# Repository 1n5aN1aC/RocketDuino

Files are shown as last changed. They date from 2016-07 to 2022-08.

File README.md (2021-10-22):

# RocketDuino
This is an Arduino Board designed for use in High-Powered model rockets.

(Picture Goes Here)

<h1>Features</h1>

 - Parachute Deployment:  Dual parachute deployment via high-power mosfets to route raw battery current directly through the ignitors.  (Designed for 9v)
 - GPS Tracking: On-board GPS used to verify hight measurements, get speed readouts, and know the location of the rocket.
 - Telemetry: LoRa telemetry transmission with a maximum range of over 8km.  This is used to relay location and height data to a ground control station to ease finding the rocket after parachute deployment.

<h1>Hardware</h1>

 - MCU: Early versions (which were flown successfully) used a wemos D1 mini.  However, the current version uses a Teensy LC as the main microcontroller.  This change was made primarily to take advantage of the multiple hardware serial ports on the Teensy line.
 - GPS:  Works with any Serial GPS device that outputs classic NMEA messages, (GPGGA, etc) does NOT currently support the newer GNGGA messages.  The PCB is designed to directly mount a uBlox NEO-M6N module.  (Note that the config needs to be changes to output GPGGA, etc)
 - Barometer:  A BMP280 is used for more accurate real-time elevation measurement.  Note that the Teensy is NOT 5v compliant, so you need the 3.3v BMP280 board.
 - Telemetry:  Data Transmission is done using a E32-433T30D 1W LoRa trasmitter, but any data transmitter with a serial interface should work, with only minor changes to the board.  (The PCB is designed to mount the module directly.)

<h3>The Board</h3>

Short Description coming soon.

[For Detailed PCB Information, click here](https://github.com/1n5aN1aC/RocketDuino/tree/master/PCB)

<h3>The Software</h3>

Short Description coming soon.

[For Detailed Arduino Information, click here](https://github.com/1n5aN1aC/RocketDuino/tree/master/Arduino)

<h3>The Results</h3>

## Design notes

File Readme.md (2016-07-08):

#PCB files
This is where the files for making the PCBare located.  We use Eagle as our development tool of choice.

##Features
Description Coming Soon!

##Design
Description Coming Soon!

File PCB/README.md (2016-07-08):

#PCB files
This is where the files for making the PCB are located.  We use Eagle as our development tool of choice.

##Features
Description Coming Soon!

##Design
Description Coming Soon!

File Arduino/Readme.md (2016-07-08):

#Arduino files
This is where the files for compiling the flight computer & the ground station are located

##Features
Description Coming Soon!

##Design
Description Coming Soon!

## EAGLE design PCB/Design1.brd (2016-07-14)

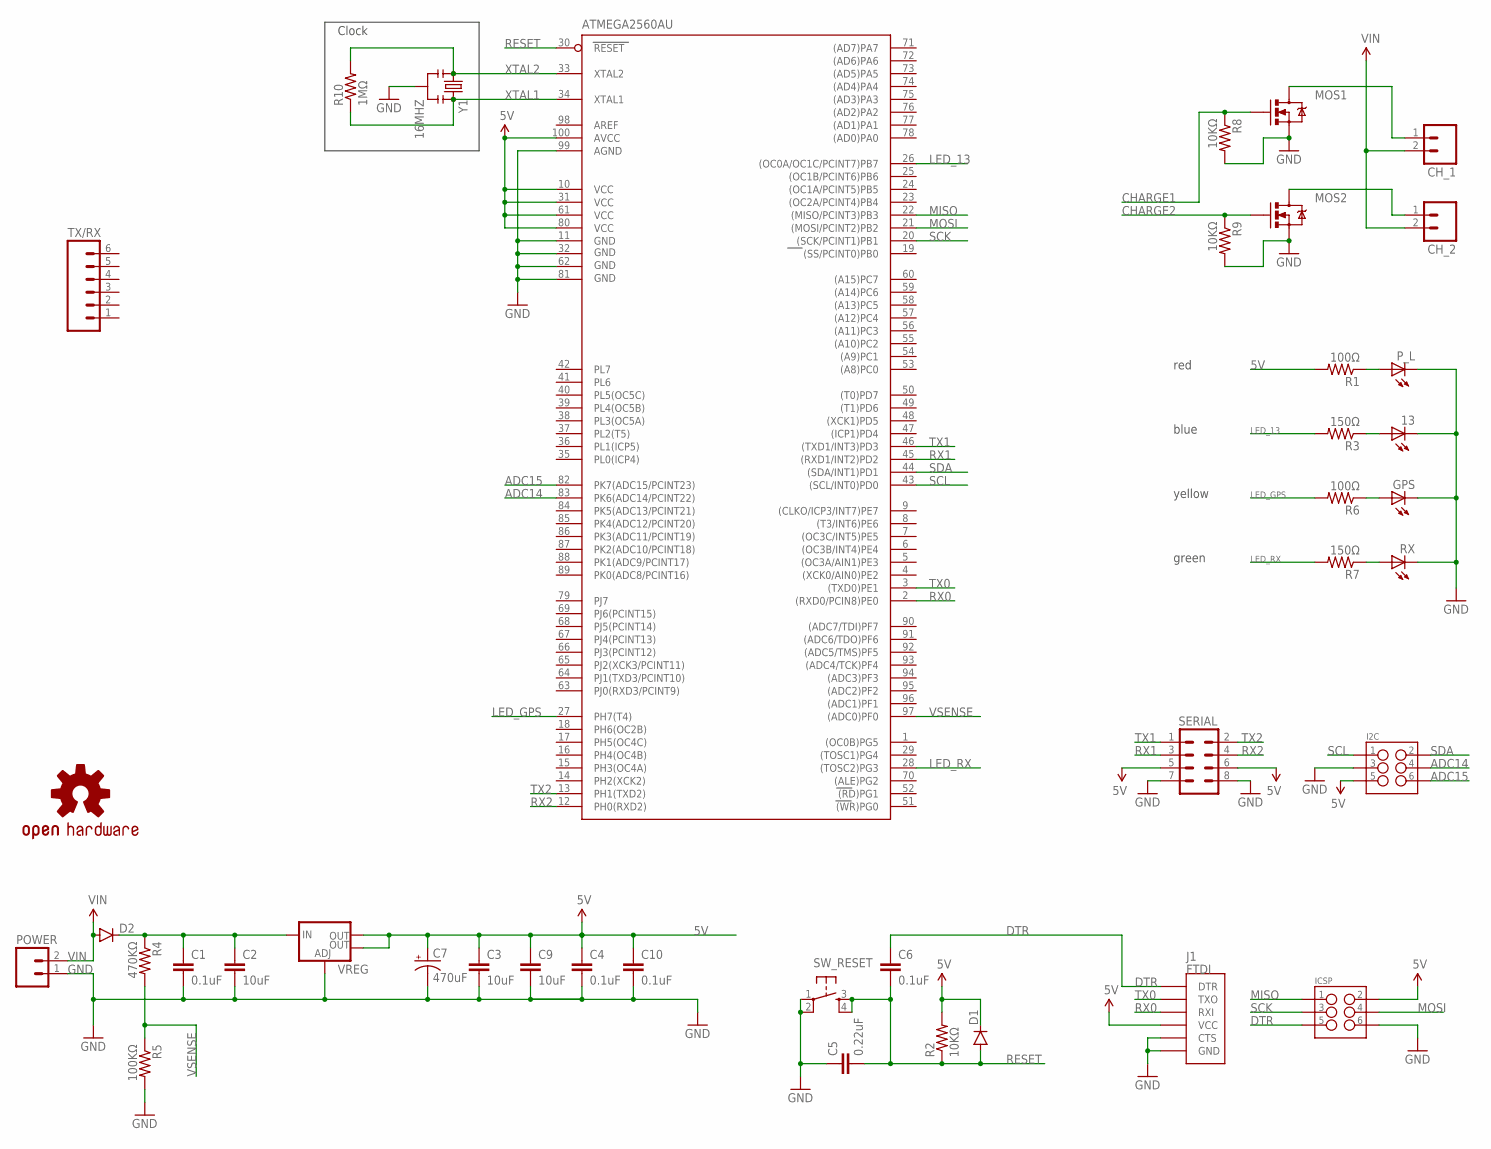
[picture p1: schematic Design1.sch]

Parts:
13: LEDSML0805; SML0805
ATMEGA2560AU: ATMEGA2560AU; TQFP100
C1, C4, C6, C10: 0.1uF; 1206
C2, C3, C9: 10uF; 1206
C5: 0.22uF; 1206
C7: 470uF; CPOL-RADIAL-100UF-25V
CH_1, CH_2: M02LOCK_LONGPADS; 1X02_LOCK_LONGPADS
D1, D2: DIODESMA-ALT; SMA-DIODE_ALT
GPS: LEDSML0805; SML0805
I2C: M03X2FEMALE_SMD; 2X3_SMD
ICSP: M03X2FEMALE_SMD; 2X3_SMD
J1: FTDI; FTDI_DEVICE_SIDE
LOGO1: OSHW-LOGOM; OSHW-LOGO-M
MOS1, MOS2: MOSFET-NCHANNELFQP30N06L; TO220V
POWER: M02LOCK_LONGPADS; 1X02_LOCK_LONGPADS
P_L: LEDSML0805; SML0805
R1, R6: 100Ω; 1206
R2, R8, R9: 10KΩ; 1206
R3, R7: 150Ω; 1206
R4: 470KΩ; 1206
R5: 100KΩ; 1206
R10: 1MΩ; 1206
RX: LEDSML0805; SML0805
SERIAL: M04X2; 2X4
SW_RESET: SWITCH_SPST_4_PINSQUARE; TACTILE-SWITCH-SMD
TX/RX: M06SILK_FEMALE_PTH; 1X06
VREG: V_REG_LM1117SOT223; SOT223
Y1: 16MHZ; RESONATOR-SMD

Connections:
5V: ATMEGA2560AU.10 (VCC), ATMEGA2560AU.31 (VCC1), ATMEGA2560AU.61 (VCC2), ATMEGA2560AU.80 (VCC3), ATMEGA2560AU.100 (AVCC), C3.1, C4.1, C7.1 (+), C9.1, C10.1, D1.C, I2C.5, ICSP.2, J1.P$4 (VCC), R1.2, R2.2, SERIAL.5, SERIAL.6, VREG.2 (OUT), VREG.4 (OUT)
ADC14: ATMEGA2560AU.83 (PK6(ADC14/PCINT22)), I2C.4
ADC15: ATMEGA2560AU.82 (PK7(ADC15/PCINT23)), I2C.6
CHARGE1: MOS1.1 (G), R8.1
CHARGE2: MOS2.1 (G), R9.1
DTR: C6.1, ICSP.5, J1.P$1 (DTR)
GND: 13.C, ATMEGA2560AU.11 (GND), ATMEGA2560AU.32 (GND1), ATMEGA2560AU.62 (GND2), ATMEGA2560AU.81 (GND3), ATMEGA2560AU.99 (AGND), C1.2, C2.2, C3.2, C4.2, C5.1, C7.2 (-), C9.2, C10.2, GPS.C, I2C.3, ICSP.6, J1.P$5 (CTS), J1.P$6 (GND), MOS1.3 (S), MOS2.3 (S), POWER.1, P_L.C, R5.2, R8.2, R9.2, RX.C, SERIAL.7, SERIAL.8, SW_RESET.1, SW_RESET.2, VREG.1 (ADJ), Y1.2
LED_13: ATMEGA2560AU.26 ((OC0A/OC1C/PCINT7)PB7), R3.2
LED_GPS: ATMEGA2560AU.27 (PH7(T4)), R6.2
LED_RX: ATMEGA2560AU.28 ((TOSC2)PG3), R7.2
MISO: ATMEGA2560AU.22 ((MISO/PCINT3)PB3), ICSP.1
MOS1: CH_1.1, MOS1.2 (D)
MOS2: CH_2.1, MOS2.2 (D)
MOSI: ATMEGA2560AU.21 ((MOSI/PCINT2)PB2), ICSP.4
unnamed: GPS.A, R6.1
unnamed: P_L.A, R1.1
unnamed: 13.A, R3.1
unnamed: R7.1, RX.A
RESET: ATMEGA2560AU.30 (RESET), C5.2, C6.2, D1.A, R2.1, SW_RESET.3, SW_RESET.4
RX0: ATMEGA2560AU.2 ((RXD0/PCIN8)PE0), J1.P$3 (RXI)
RX1: ATMEGA2560AU.45 ((RXD1/INT2)PD2), SERIAL.3
RX2: ATMEGA2560AU.12 (PH0(RXD2)), SERIAL.4
SCK: ATMEGA2560AU.20 ((SCK/PCINT1)PB1), ICSP.3
SCL: ATMEGA2560AU.43 ((SCL/INT0)PD0), I2C.1
SDA: ATMEGA2560AU.44 ((SDA/INT1)PD1), I2C.2
TX0: ATMEGA2560AU.3 ((TXD0)PE1), J1.P$2 (TXO)
TX1: ATMEGA2560AU.46 ((TXD1/INT3)PD3), SERIAL.1
TX2: ATMEGA2560AU.13 (PH1(TXD2)), SERIAL.2
VIN: CH_1.2, CH_2.2, D2.A, POWER.2
VIN_RECTIFIED: C1.1, C2.1, D2.C, R4.1, VREG.3 (IN)
VSENSE: ATMEGA2560AU.97 ((ADC0)PF0), R4.2, R5.1
XTAL1: ATMEGA2560AU.34 (XTAL1), R10.1, Y1.3
XTAL2: ATMEGA2560AU.33 (XTAL2), R10.2, Y1.1

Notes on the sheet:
Clock
green
yellow
blue
red

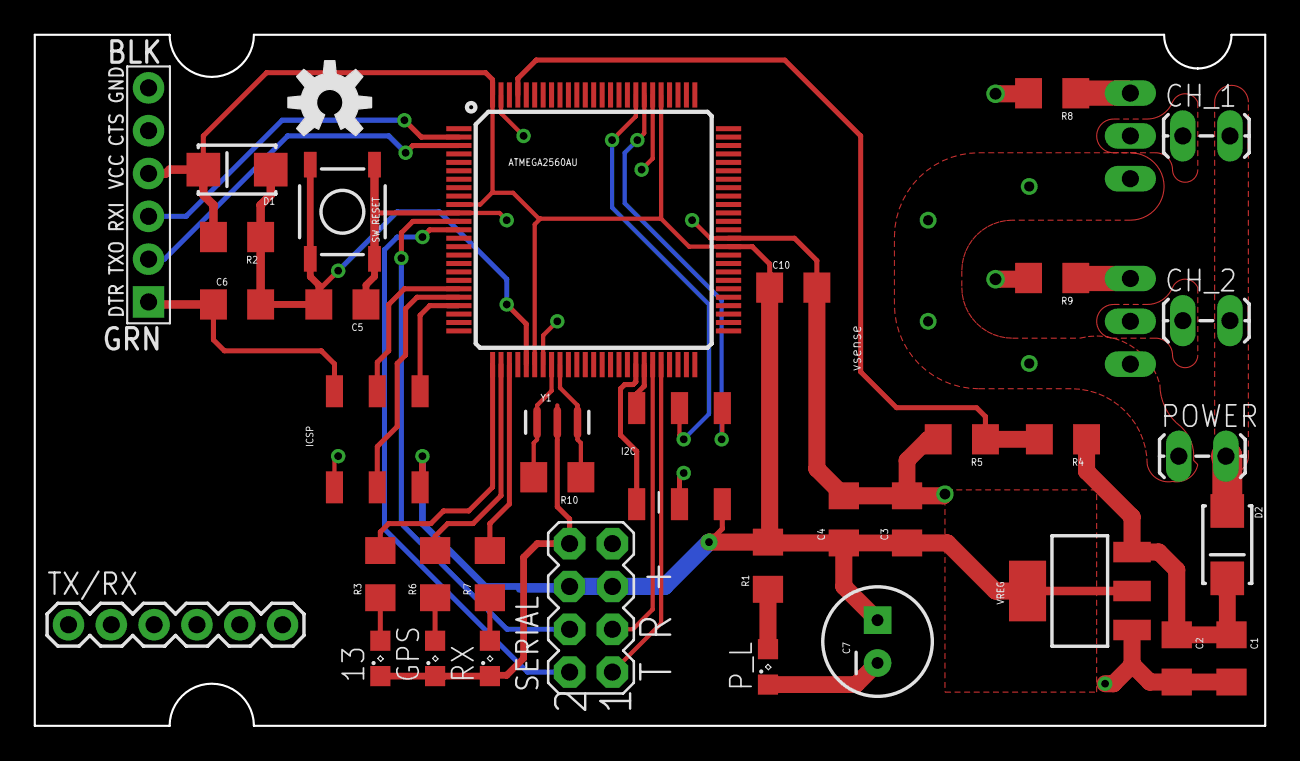
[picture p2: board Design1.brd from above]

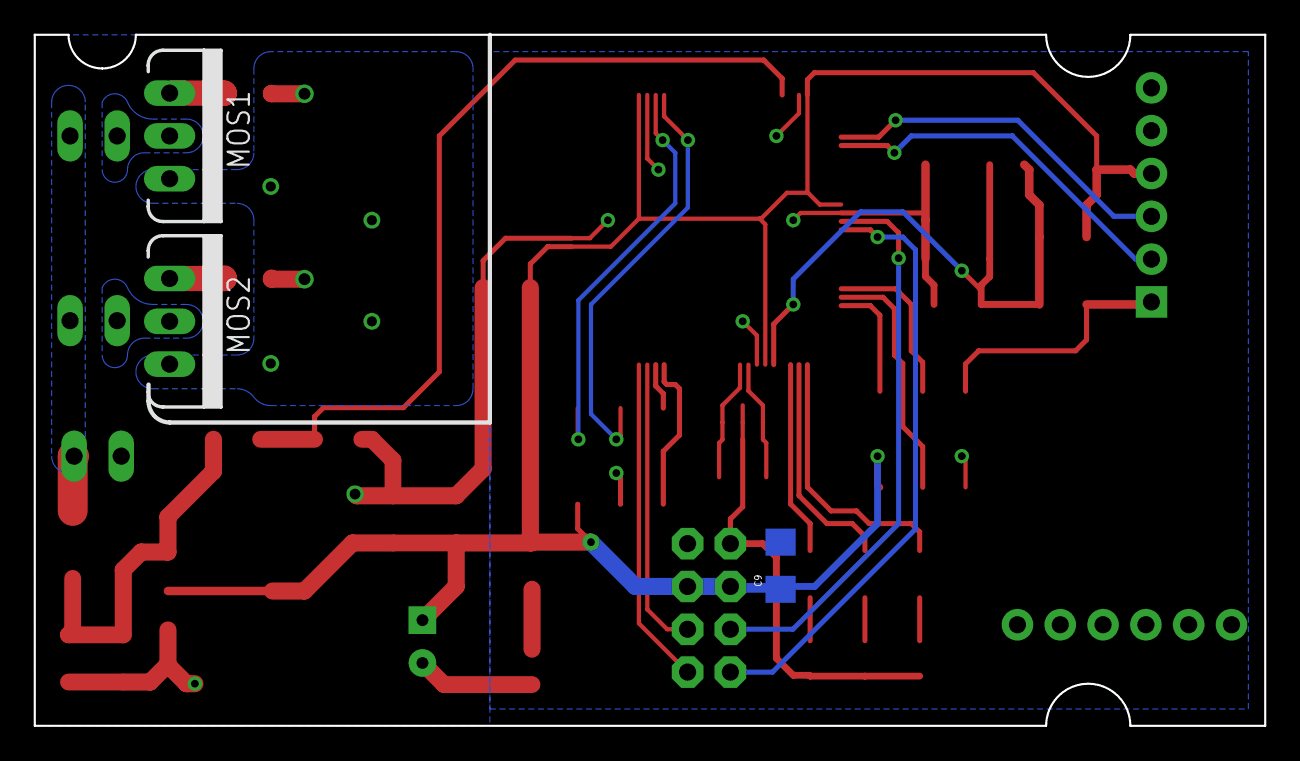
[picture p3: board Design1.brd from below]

Board: 2 copper layers, 73.0 x 41.0 mm, 40 parts (3 on the bottom side), 33 nets.

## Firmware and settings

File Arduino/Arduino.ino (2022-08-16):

//
// File:    main.ino
// Author:  1n5aN1aC (Joshua Villwock)
// Purpose: Handles all logic for the RocketDuino
//
// TODO:
// 1. Increase transmission power to maximum.  (is min right now)
// 2. Mode for Serial Passthrough to GPS.  (To upload sat info, etc.)
//

#include "Arduino.h"
#include <Wire.h>
#include <BMP280_DEV.h>
#include <SimpleKalmanFilter.h>
#include <TinyGPS++.h>

//LoRa Hardware parameters
#define E32_TTL_1W
#define FREQUENCY_433
#include "LoRa_E32.h"

// Pin designations
#define BUZZER 17 //Buzzer Pin
#define CHUTE1 6  //Output for Chute Channel 1
#define CHUTE2 5  //Output for Chute Channel 2
#define LED    13 //Teensy Onboard LED
#define LED1   4  //PCB LED 1 (Green)
#define LED2   3  //PCD LED 2 (Yellow)
#define LORARX 9  //Lora_RX  (E32TX)
#define LORATX 10 //Lora_TX  (E32RX)
#define LORAUX 8  //Lora_AUX (Status)
#define LORAM0 12 //Lora_M0  (Mode Set)
#define LORAM1 11 //Lora_M1  (Mode Set)
//GPS  = Serial1
//Lora = Serial2

// Barometer Variables
BMP280_DEV bmp280; // Define barometer object. Basic I2C SCL & SDA
SimpleKalmanFilter altitudeFilterObject(4, 1, 0.015); //Measurement Uncertainty, Estimation Uncertainty, Noise
float    temporaryAltitude       = 0;
float    currentFilteredAltitude = 0;
elapsedMillis lastBarometerRead;

// Mode variables
#define  FREQUENCY_UPDATE_MODE   250
uint8_t  currentMode             = 0;
elapsedMillis lastModeUpdate;

// Buzzer Variables
#define  FREQUENCY_UPDATE_BUZZER 3000
elapsedMillis lastBuzzerUpdate;

// Serial Variables
#define  FREQUENCY_TX_LORA       1000
elapsedMillis lastLoraTX;
LoRa_E32 e32ttl100(LORARX, LORATX, LORAUX, LORAM0, LORAM1, UART_BPS_RATE_9600);

// GPS Variables
TinyGPSPlus   gps;
TinyGPSCustom gpsStatus(gps, "GPGGA", 6);
#define  GPSBAUDRATE             115200
unsigned char extraSerialBuffer  [300];   //extra memory to dedocate to gps rx
int sizeOfExtraSerialBuffer      = 300;
bool     GPSforward              = false;
elapsedMillis lastGPSReceive;

struct __attribute__((packed)) packet_normal {
  uint32_t timeStamp;         //4 bytes
  uint8_t  currentMode;       //1 byte
  int16_t  currentAlt;        //2 bytes
  int16_t  startingAlt;       //2 bytes
  int16_t  maxAlt;            //2 bytes
  
  double   latitude;          //8 bytes
  double   longitude;         //8 bytes
  uint16_t gpsAlt;            //2 bytes
  uint16_t gpsSpeedMPS;       //2 bytes
  uint8_t  gpsSats;           //1 byte
  uint16_t gpsHDOP;           //2 bytes
  uint8_t  gps_mode;          //1 byte (only 2 bits needed)
  uint8_t  gps_valid;         //1 byte (only 1 bit needed)
  uint16_t gps_receivedSents; //2 bytes
  uint8_t  gps_checkFails;    //1 byte
  uint8_t  checksum;          //1 byte
};                   //TOTAL = 40 bytes, maximum 51 / 58 Bytes   (58 on-air) [Must wait 3-byte time between packets if <58bytes]

// Init Values
int16_t  maxAltitudeSeen    = -32768;   //Highest we've been to
int16_t  startingAltitude   = 0;   //what elevation we consider 'ground'
uint16_t failsafeAltitude   = 100; //minimum alt we need to reach to arm
uint8_t  extraDeploymentAlt = 25;  //Extra meters we have to fall below max alt before deployment (to be safe from jiggle)

//
// Run Initial setup Tasks
//
void setup() {
  // Init variables & objects
  pinMode(BUZZER, OUTPUT);
  pinMode(CHUTE1, OUTPUT);
  pinMode(CHUTE2, OUTPUT);
  pinMode(LED,    OUTPUT);
  pinMode(LED1,   OUTPUT);
  pinMode(LED2,   OUTPUT);
  pinMode(LORAM0, OUTPUT);
  pinMode(LORAM1, OUTPUT);
  digitalWrite(LED,    HIGH);  //LED on startup

  //Init USB serial port
  Serial.begin(57600); //USB
  Serial.println(F("[SER]  (USB)    Debug serial began.  (57600)"));

  //Init GPS serial port
  Serial1.begin(GPSBAUDRATE);
  Serial.println(F("[SER]  (GPS)    Gps serial began.") + String(GPSBAUDRATE) + ")");
  //We need to dedicate extra memory to the GPS receive buffer:
  Serial1.addMemoryForRead(extraSerialBuffer, sizeOfExtraSerialBuffer);

  //Init lora transmitter
  setup_LoRa();

  //Init Baro
  Serial.println(F("[BARO] (Config) Configuring Altimiter..."));
  bmp280.begin(SLEEP_MODE, BMP280_I2C_ALT_ADDR);  // Default initialisation with alternative I2C address (0x76), place the BMP280 into SLEEP_MODE
  bmp280.setPresOversampling(OVERSAMPLING_X2);    // Options are OVERSAMPLING_SKIP, _X1, _X2, _X4, _X8, _X16
  bmp280.setTempOversampling(OVERSAMPLING_X1);    // Options are OVERSAMPLING_SKIP, _X1, _X2, _X4, _X8, _X16
  bmp280.setIIRFilter(IIR_FILTER_OFF);            // Options are IIR_FILTER_OFF, _2, _4, _8, _16
  bmp280.setTimeStandby(TIME_STANDBY_62MS);       // Options are TIME_STANDBY_05MS, _62MS, _125MS, _250MS, _500MS, _1000MS, 2000MS, 4000MS
  bmp280.startNormalConversion();                 // Start BMP280 continuous conversion in NORMAL_MODE

  delay(500); //Wait for stuff to init
  digitalWrite(LED, LOW);  //LED off as startup finished
  Serial.println("[Info]          Start up Complete.");
}

void setup_LoRa() {
  //Serial2.begin(LORABAUDRATE);
  //Serial.println("LORA Serial Started" + String(LORABAUDRATE) + ")");

  //Connect to module
  Serial.println(F("[LoRa] (Config) Connecting to module..."));  // https://www.mischianti.org/2019/10/21/lora-e32-device-for-arduino-esp32-or-esp8266-library-part-2/
  e32ttl100.begin();                                             // Startup all pins and UART
  delay(200);

  //Fetch LoRa module information
  ResponseStructContainer cMi;
  cMi = e32ttl100.getModuleInformation();
  ModuleInformation mi = *(ModuleInformation*)cMi.data; // It's important get information pointer before all other operation
  cMi.close();
  Serial.print(F("[LoRa] (Config) Version:  "));
  Serial.println(mi.version, HEX);
  Serial.print(F("[LoRa] (Config) Features: "));
  Serial.println(mi.features, HEX);

  Serial.println(F("[LoRa] (Config) Fetching current config..."));
  ResponseStructContainer c;                                     // C stores the config
  c = e32ttl100.getConfiguration();                              // Load config from module
  Configuration configuration = *(Configuration*) c.data;        // Make local config object
  int numChanges = 0;

  //Communication channel (def 17H == 23d == 433MHz / 410 M + CHAN*1M)
  Serial.print(F("[LoRa] (Config) Communication channel: "));
  Serial.print(configuration.CHAN, HEX);
  Serial.print(F(" Wants: "));
  Serial.print(0x17, HEX);
  if (configuration.CHAN != 0x17) {
    configuration.CHAN = 0x17;
    numChanges++;
    Serial.print(F(" OPTION UPDATED."));
  }
  Serial.println();

  //Forward Error Correction
  Serial.print(F("[LoRa] (Config) FEC: "));
  Serial.print(configuration.OPTION.fec);
  Serial.print(F(" Wants: "));
  Serial.print(FEC_1_ON);
  if (configuration.OPTION.fec != FEC_1_ON) {
    configuration.OPTION.fec = FEC_1_ON;
    numChanges++;
    Serial.print(F(" OPTION UPDATED."));
  }
  Serial.println();

  //Broadcast/directed setting
  Serial.print(F("[LoRa] (Config) Fixed/Transparent: "));
  Serial.print(configuration.OPTION.fixedTransmission);
  Serial.print(F(" Wants: "));
  Serial.print(FT_FIXED_TRANSMISSION);
  if (configuration.OPTION.fixedTransmission != FT_FIXED_TRANSMISSION) {
    configuration.OPTION.fixedTransmission = FT_FIXED_TRANSMISSION;
    numChanges++;
    Serial.print(F(" OPTION UPDATED."));
  }
  Serial.println();

  //Pull ups enabled or not
  Serial.print(F("[LoRa] (Config) Pull-ups: "));
  Serial.print(configuration.OPTION.ioDriveMode);
  Serial.print(F(" Wants: "));
  Serial.print(IO_D_MODE_PUSH_PULLS_PULL_UPS);
  if (configuration.OPTION.ioDriveMode != IO_D_MODE_PUSH_PULLS_PULL_UPS) {
    configuration.OPTION.ioDriveMode = IO_D_MODE_PUSH_PULLS_PULL_UPS;
    numChanges++;
    Serial.print(F(" OPTION UPDATED."));
  }
  Serial.println();

  //dBm transmission power (POWER_30 POWER_27 POWER_24 POWER_21)
  Serial.print(F("[LoRa] (Config) TX Power: "));
  Serial.print(configuration.OPTION.transmissionPower);
  Serial.print(F(" Wants: "));
  Serial.print(POWER_21);
  if (configuration.OPTION.transmissionPower != POWER_21) {
    configuration.OPTION.transmissionPower = POWER_21;
    numChanges++;
    Serial.print(F(" OPTION UPDATED."));
  }
  Serial.println();

  //Wait time for wake up
  Serial.print(F("[LoRa] (Config) Wake time: "));
  Serial.print(configuration.OPTION.wirelessWakeupTime);
  Serial.print(F(" Wants: "));
  Serial.print(WAKE_UP_250);
  if (configuration.OPTION.wirelessWakeupTime != WAKE_UP_250) {
    configuration.OPTION.wirelessWakeupTime = WAKE_UP_250;
    numChanges++;
    Serial.print(F(" OPTION UPDATED."));
  }
  Serial.println();

  //Air data rate (2.4k)
  Serial.print(F("[LoRa] (Config) Air data rate: "));
  Serial.print(configuration.SPED.airDataRate);
  Serial.print(F(" Wants: "));
  Serial.print(AIR_DATA_RATE_010_24);
  if (configuration.SPED.airDataRate != AIR_DATA_RATE_010_24) {
    configuration.SPED.airDataRate = AIR_DATA_RATE_010_24;
    numChanges++;
    Serial.print(F(" OPTION UPDATED."));
  }
  Serial.println();

  //Serial baud rate
  Serial.print(F("[LoRa] (Config) Serial Baud: "));
  Serial.print(configuration.SPED.uartBaudRate);
  Serial.print(F(" Wants: "));
  Serial.print(UART_BPS_9600);
  if (configuration.SPED.uartBaudRate != UART_BPS_9600) {
    configuration.SPED.uartBaudRate = UART_BPS_9600;
    numChanges++;
    Serial.print(F(" OPTION UPDATED."));
  }
  Serial.println();

  //Serial UART Parity
  Serial.print(F("[LoRa] (Config) Serial Parity: "));
  Serial.print(configuration.SPED.uartParity);
  Serial.print(F(" Wants: "));
  Serial.print(MODE_00_8N1);
  if (configuration.SPED.uartParity != MODE_00_8N1) {
    configuration.SPED.uartParity = MODE_00_8N1;
    numChanges++;
    Serial.print(F(" OPTION UPDATED."));
  }
  Serial.println();

  //Address(high)
  Serial.print(F("[LoRa] (Config) Address (high): "));
  Serial.print(configuration.ADDH);
  Serial.print(F(" Wants: "));
  Serial.print(13);
  if (configuration.ADDH != 13) {
    configuration.ADDH = 13;
    numChanges++;
    Serial.print(F(" OPTION UPDATED."));
  }
  Serial.println();

  //Address(low)
  Serial.print(F("[LoRa] (Config) Address (low): "));
  Serial.print(configuration.ADDL);
  Serial.print(F(" Wants: "));
  Serial.print(13);
  if (configuration.ADDL != 13) {
    configuration.ADDL = 13;
    numChanges++;
    Serial.print(F(" OPTION UPDATED."));
  }
  Serial.println();

  if (numChanges > 0) {
    Serial.println(F("[LoRa] (Config) Setting new config..."));
    e32ttl100.setConfiguration(configuration, WRITE_CFG_PWR_DWN_SAVE); // Save config permanently
    delay(500); //Wait for stuff to save and such
  } else {
    Serial.println(F("[LoRa] (Config) No config changes to save..."));
  }
  c.close();                                                         // Must close after opening

  delay(300); //Wait for stuff to init
  Serial.println(F("[LoRa] (Config) Complete."));
}

//
// Main Loop Tasks
//
void loop() {
  //Gather new (baro) data
  update_barometer();

  //Calculate on data (flight modes)
  calculate_mode();

  //Update Serial / wireless
  update_lora_send();

  //Handle incoming gps data
  update_gps_receive();

  //Handle incoming lora packets
  update_lora_receive();

  //Update buzzer / LEDs
  update_buzzer();
}

//
// Queries the barometer for elevation, stores it, and updates the running average
void update_barometer() {
  if (bmp280.getAltitude(temporaryAltitude)) {   // Check if the measurement is complete
    currentFilteredAltitude = altitudeFilterObject.updateEstimate(temporaryAltitude);

    //Update max altitude if needed and out of startup mode
    if (currentMode > 0 && currentFilteredAltitude > maxAltitudeSeen) {
      maxAltitudeSeen = currentFilteredAltitude;
    }

    //Take note that we've sucessfully read the altitude:
    lastBarometerRead = 0;
  }
}

//
// Mode 0 = Boot
// Mode 1 = Below Failsafe Alt
// Mode 2 = Flying
// Mode 3 = Eject!
//
void calculate_mode() {
  if (lastModeUpdate > FREQUENCY_UPDATE_MODE) {
    lastModeUpdate = 0;

    // Mode 0 = Boot
    if (currentMode == 0) {
      //Once 20 seconds have passed on boot, lets call that the starting height.
      if (millis() > 30000) {
        startingAltitude = currentFilteredAltitude;
        currentMode = 1;
        Serial.println(F("[MODE] (Change) Mode 0->1"));
        digitalWrite(LED, LOW); //Onboard LED
      }
      //Also, if we haven't read the barometer recently, abort:
      if (millis() > 5000 && lastBarometerRead > 5000) {
        Serial.println(F("[ERROR]         More than 5000ms since last baro read!"));
        tone(BUZZER, 4000);
        digitalWrite(LED, HIGH);  //LED on error
        delay(90000);
      }
      return;
    }

    //Mode 1 = Below Failsafe Alt
    if (currentMode == 1) {
      //If we are above the failsafe height, go to flight mode.
      if (currentFilteredAltitude > startingAltitude + failsafeAltitude) {
        currentMode = 2;
        Serial.println(F("[MODE] (Change) Mode 1->2"));
      }
      return;
    }

    //Mode 2 = Flying
    if (currentMode == 2) {
      //If we're more than the safety distance below max alt, go to eject mode
      if (maxAltitudeSeen > currentFilteredAltitude + extraDeploymentAlt) {
        //WAIT!! If we're below the failsafe altitude, don't.
        if (currentFilteredAltitude < startingAltitude + failsafeAltitude) {
          return;
        }
        currentMode = 3;
        Serial.println(F("[MODE] (Change) Mode 2->3"));
        digitalWrite(CHUTE1, HIGH);
        digitalWrite(CHUTE2, HIGH);
        delay(500);
        digitalWrite(CHUTE1, LOW);
        digitalWrite(CHUTE2, LOW);
      }
      return;
    }

    //Mode 3 = Eject & Recovery
    if (currentMode == 3) {
      //We're already done, so do nothing I guess?
    }
  }
}

//Process any incoming bytes from the GPS
void update_gps_receive() {
  while (Serial1.available()) {
    gps.encode(Serial1.read());
    lastGPSReceive = 0;
  }
}

// Buzzes depending on current mode
// Updates GPSmode led
// Updates flight mode LED
void update_buzzer() {
  if (lastBuzzerUpdate > FREQUENCY_UPDATE_BUZZER) {
    //Update buzzer
    lastBuzzerUpdate = 0;
    if (currentMode == 0) {
      digitalWrite(LED1, HIGH); // Status LED on for duration
      tone(BUZZER, 2000, 75);   // Send 2KHz sound signal for 75ms
      delay(125);
      tone(BUZZER, 4000, 75);   // Send 4KHz sound signal for 75ms
      delay(125);
      tone(BUZZER, 2000, 25);   // Send 2KHz sound signal for 25ms
      digitalWrite(LED1, LOW);
    } else if (currentMode == 1) {
      digitalWrite(LED1, HIGH); // Status LED on
      tone(BUZZER, 4000, 25);   // Send 4KHz sound signal for 25ms
    } else if (currentMode == 3) {
      digitalWrite(LED1, LOW);  // Status LED off
      tone(BUZZER, 4000, 100);  // Send 4KHz sound signal for 100ms
      delay(200);
      tone(BUZZER, 4000, 100);  // Send 4KHz sound signal for 100ms
    }

    //Update GPSmode LED
    uint8_t gps_mode;
    if (gps.location.age() > 1500) {
      gps_mode = 0;
    } else {
      gps_mode = atoi(gpsStatus.value());
    }
    if (gps_mode == 2) {        //DGPS
      digitalWrite(LED2, HIGH);
    } else if (gps_mode == 1) { //2D-3D Fix
      bool current = digitalRead(LED2);
      if (current) {
        digitalWrite(LED2, LOW);
      } else {
        digitalWrite(LED2, HIGH);
      }
    } else {                    //No fix
      digitalWrite(LED2, LOW);
    }
  }
}

void update_lora_receive() {
  while (Serial2.available()) {
    byte b = Serial2.read();
  }
}

void update_lora_send() {
  if (lastLoraTX > FREQUENCY_TX_LORA) {
    lastLoraTX = 0;

    send_packet_normal();
  }
}

void send_packet_normal() {
  //When was the last time we got GPS packets?
  uint8_t gps_valid = 0;
  if (gps.altitude.age() > 1050) {
    gps_valid += 1;    //TinyGPS++ says it wasn't updated within last second.
  }
  if (lastGPSReceive > 1000) {
    gps_valid += 2;    //We haven't received any gps serial to even pass it on to TinyGPS++.
  }
  if (!gps.altitude.isValid()) {
    gps_valid += 4;    //Something wrong with the altitude fix?
  }

//  Serial.print(F("[DEBUG] "));
//  Serial.print(static_cast<int16_t>(currentFilteredAltitude));
//    Serial.print(",");
//  Serial.print(maxAltitudeSeen);
//    Serial.print(",");
//  Serial.print(startingAltitude);
//    Serial.print(",");
//  Serial.print(currentMode);
//    Serial.print(",");
//  Serial.print(gps.location.lat());
//    Serial.print(",");
//  Serial.print(gps.location.lng());
//    Serial.print(",");
//  Serial.print(gps.altitude.meters());
//    Serial.print(",");
//  Serial.print(gps.speed.mps());
//    Serial.print(",");
//  Serial.print(gps.satellites.value());
//    Serial.print(",");
//  Serial.print(static_cast<int16_t>(gps.hdop.value()));
//    Serial.print(",");
//  Serial.print(gpsStatus.value());
//    Serial.print(",");
//  Serial.print(gps_valid);
//  Serial.println();

  packet_normal packet = {
    millis(),
    currentMode,
    static_cast<int16_t>(currentFilteredAltitude),
    startingAltitude,
    maxAltitudeSeen,
    gps.location.lat(),
    gps.location.lng(),
    static_cast<uint16_t>(gps.altitude.meters()),
    static_cast<uint16_t>(gps.speed.mps()),
    static_cast<uint8_t> (gps.satellites.value()),
    static_cast<uint16_t>(gps.hdop.value()),
    static_cast<uint8_t> (String(gpsStatus.value()).toInt()),
    gps_valid,
    static_cast<uint16_t>(gps.passedChecksum()),
    static_cast<uint8_t> (gps.failedChecksum()),
    0 //checksum
  };
  //Serial.println(sizeof(packet));

  //Calculate checksum and add to packet
  uint8_t sum = 0;
  uint8_t *p = (uint8_t *)&packet;
  for (uint8_t i=0; i<sizeof(packet); i++) {
      sum += p[i];
  }
  packet.checksum = sum;

  //Serial.write(reinterpret_cast<char*>(&packet), sizeof packet);
  //Serial2.write(reinterpret_cast<char*>(&packet), sizeof packet);
  e32ttl100.sendFixedMessage(0,3,0x17,&packet, sizeof(packet));
}

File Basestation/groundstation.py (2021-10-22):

#!/usr/bin/python
import signal, sys, time, os, datetime
import serial, curses, pickle
import bitstring, numpy
import matplotlib.pyplot as plt

ser = serial.Serial(port='com5', baudrate=57600, timeout=0.1)
ser.flushInput()

data_dict = {'altitude':0, 'altitude_starting':0, 'altitude_max':0,'mode':0}
data_dict['gps'] = {'altitude':0, 'lat':0, 'long':0, 'speed':0, 'sats':0, 'mode':0, 'recent':0}
data_dict['ground_stats'] = {'num_pks_basic':0, 'num_pks_gps':0, 'num_pks_extra':0, 'num_pks_unknown':0}

#logfile naming
dt = datetime.datetime.now()
fileName = 'Data-%s-%s-%s_%s-%s-%s.csv' % (dt.year, dt.month, dt.day, dt.hour, dt.minute, dt.second)
log_file = open(fileName, "w")

last_basic   = time.time()
last_gps     = time.time()
last_extra   = time.time()
last_unknown = time.time()

#adjust these values based on your location and map, lat and long are in decimal degrees
#TRX = -123.33515659247273 #top right longitude
#TRY = 44.983171093204625  #top right latitude
#BLX = -123.33956613486257 #bottom left longitude
#BLY = 44.98096497612233   #bottom left latitude
TRX = -123.3367622         #top right longitude
TRY = 45.0113628           #top right latitude
BLX = -123.3450571         #bottom left longitude 0.006611
BLY = 45.0073493           #bottom left latitude  0.0027238
last_lat = TRY

#Set up the Map:
plt.ion #interactive mode
#im = plt.imread('home.png') #lay the image under the graph
im = plt.imread('buhler.png') #lay the image under the graph
implot = plt.imshow(im,extent=[BLX, TRX, BLY, TRY]) #read a png file to map on
#Joshua:
path_collection = []
plt.draw()
plt.pause(0.05) #is necessary for the plot to update for some reason

def update_screen(screen):
	screen.clear()
	screen.border(0)
	
	#Header
	screen.addstr(2, 4, "RocketDuino Ground Control Station", curses.color_pair(1))
	screen.addstr(3, 16, "v 0.2.1", curses.color_pair(1))
	
	#Mode
	screen.addstr(6, 6, "MODE:      ", curses.color_pair(2))
	screen.addstr(6, 17, str(data_dict['mode']))
	if   data_dict['mode'] == 0:
		screen.addstr(6, 19, str("(Warmup)"), curses.color_pair(7))
	elif data_dict['mode'] == 1:
		screen.addstr(6, 19, str("(Ready)"), curses.color_pair(6))
	elif data_dict['mode'] == 2:
		screen.addstr(6, 19, str("(Flying)"), curses.color_pair(8))
	elif data_dict['mode'] == 3:
		screen.addstr(6, 19, str("(Recovery)"), curses.color_pair(7))
	
	screen.addstr(7, 6, "GPS MODE:  ", curses.color_pair(2))
	screen.addstr(7, 17, str(data_dict['gps']['mode']))
	#GpsMode:
	if   data_dict['gps']['mode'] == 0:
		screen.addstr(7, 19, str("(No Fix)"), curses.color_pair(7))
	elif data_dict['gps']['mode'] == 1:
		screen.addstr(7, 19, str("(2D/3D)"), curses.color_pair(8))
	elif data_dict['gps']['mode'] == 2:
		screen.addstr(7, 19, str("(DGPS)"), curses.color_pair(6))
	elif data_dict['gps']['mode'] == 3:
		screen.addstr(7, 19, str("(Bad Fix)"), curses.color_pair(7))
	screen.addstr(" (" + str(data_dict['gps']['sats']) + " sats) ", curses.color_pair(3))
	
	#GpsRecent:
	if   data_dict['gps']['recent'] == 0:
		screen.addstr(str("(GPS Disconnected)"), curses.color_pair(7))
	
	#Altitude measurements:
	screen.addstr(10, 6, "max alt:   ", curses.color_pair(2))
	screen.addstr(11, 6, "altitude:  ", curses.color_pair(2))
	screen.addstr(12, 6, "start alt: ", curses.color_pair(2))
	
	screen.addstr(10, 17, str(data_dict['altitude_max']))
	screen.addstr(" (m)", curses.color_pair(3))
	screen.addstr(11, 17, str(data_dict['altitude']))
	screen.addstr(" (m)", curses.color_pair(3))
	screen.addstr(12, 17, str(data_dict['altitude_starting']))
	screen.addstr(" (m)", curses.color_pair(3))
	
	screen.addstr(10, 26, str(round(data_dict['altitude_max'] * 3.28)))
	screen.addstr(" (ft)", curses.color_pair(3))
	screen.addstr(11, 26, str(round(data_dict['altitude'] * 3.28)))
	screen.addstr(" (ft)", curses.color_pair(3))
	screen.addstr(12, 26, str(round(data_dict['altitude_starting'] * 3.28)))
	screen.addstr(" (ft)", curses.color_pair(3))
	
	#Now above ground level:
	screen.addstr(10, 37, "agl: ", curses.color_pair(2))
	screen.addstr(11, 37, "agl: ", curses.color_pair(2))
	
	screen.addstr(10, 42, str(data_dict['altitude_max'] - data_dict['altitude_starting']))
	screen.addstr(" (m)", curses.color_pair(3))
	screen.addstr(11, 42, str(data_dict['altitude'] - data_dict['altitude_starting']))
	screen.addstr(" (m)", curses.color_pair(3))
	
	screen.addstr(10, 51, str(round((data_dict['altitude_max'] - data_dict['altitude_starting']) * 3.28)))
	screen.addstr(" (ft)", curses.color_pair(3))
	screen.addstr(11, 51, str(round((data_dict['altitude'] - data_dict['altitude_starting']) * 3.28)))
	screen.addstr(" (ft)", curses.color_pair(3))
	
	#GPS DATA
	screen.addstr(14, 6, "GPS DATA: ", curses.color_pair(2))
	screen.addstr(15, 6, "altitude: ", curses.color_pair(2))
	screen.addstr(16, 6, "speed:    ", curses.color_pair(2))
	screen.addstr(17, 6, "lat:      ", curses.color_pair(2))
	screen.addstr(18, 6, "long:     ", curses.color_pair(2))
	
	screen.addstr(15, 17, str(data_dict['gps']['altitude']))
	screen.addstr(" (m)", curses.color_pair(3))
	screen.addstr(16, 17, str(data_dict['gps']['speed']))
	screen.addstr(" (m/s)", curses.color_pair(3))
	screen.addstr(17, 17, str(round(data_dict['gps']['lat'], 7)))
	screen.addstr(18, 17, str(round(data_dict['gps']['long'], 7)))
	
	screen.addstr(15, 28, str(round(data_dict['gps']['altitude'] * 3.28)))
	screen.addstr(" (ft)", curses.color_pair(3))
	screen.addstr(16, 28, str(round(data_dict['gps']['speed'] * 2.237)))
	screen.addstr(" (mph)", curses.color_pair(3))
	
	#Received Packets
	screen.addstr(20, 6, "Basic Packet: ", curses.color_pair(1))
	screen.addstr(str(data_dict['ground_stats']['num_pks_basic']))
	if ((time.time() - last_basic) > 1.5):
		screen.addstr(" (" + str(round(time.time() - last_basic, 1)) + "s ago)")
	
	screen.addstr(21, 6, "  GPS Packet: ", curses.color_pair(1))
	screen.addstr(str(data_dict['ground_stats']['num_pks_gps']))
	if ((time.time() - last_gps) > 3):
		screen.addstr(" (" + str(round(time.time() - last_gps, 1)) + "s ago)")
	
	screen.addstr(22, 6, "     Unknown: ", curses.color_pair(5))
	screen.addstr(str(data_dict['ground_stats']['num_pks_unknown']))
	if ((time.time() - last_unknown) < 60):
		screen.addstr(" (" + str(round(time.time() - last_unknown, 1)) + "s ago)")
	
	#screen.addstr(19, 6, "Last Packet:")
	#screen.addstr(19, 6, "Last Packet:")
	#screen.addstr(19, 6, "Last Packet:")
	
	screen.addstr(25, 2, "Please enter a command...", curses.color_pair(1))
	screen.addstr(26, 4, "1 - Dump all current data as pickle", curses.color_pair(1))
	screen.addstr(27, 4, "q - Quit Ground Control", curses.color_pair(1))
	
	#Return after 1ms and get more data
	screen.timeout(1)
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

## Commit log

2016-07-08 Add Eagle PCB Files
    [Design1.brd, Design1.sch]
2016-07-08 Add original Arduino code
2016-07-08 Add readme page for PCB
2016-07-08 add readme for Arduino code
2016-07-08 Update new Schematic
    [Design1.sch]
2016-07-08 Update new Board
    [Design1.brd]
2016-07-09 Added battery voltage sensing; Clean up of code
    Also had to rename file to get the Arduino suite to edit it :/
2016-07-09 last nights' Schematic updates
    [Design1.sch]
2016-07-10 Add ICSP & Organize LEDs
    [Design1.brd, Design1.sch]
2016-07-10 Ad LEDS, begin work on MOSFETs
    [Design1.brd, Design1.sch]
2016-07-10 Place mosfets
    [Design1.brd, Design1.sch]
2016-07-10 switch to SMT 5v regulators
    [Design1.brd, Design1.sch]
2016-07-11 Remove 3.3v; clean up Ground near MOSFETS
    [Design1.sch]
2016-07-11 Remove 3.3v; clean up Ground near MOSFETS #2
    [Design1.brd]
2016-07-12 Move componets to (hopefully) final location
    [Design1.brd, Design1.sch]
2016-07-12 DTR fix
    [Design1.sch]
2016-07-12 Finalize part locations; Route most of the traces
    [Design1.brd]
2016-07-12 Finalize part locations; Route most of the traces 2
    [Design1.sch]
2016-07-13 Finish routing traces
    [Design1.brd]
2016-07-13 minor fixes
    [Design1.brd]
2016-07-13 Finish routing. Minor changes
    [Design1.brd]
2016-07-13 Whoops. fix that.
    [Design1.brd]
2016-07-13 Finish routing. Minor changes 2
    [Design1.sch]
2016-07-14 Add support for ground station pings
2016-07-14 Removed 1x 5v regulator; relabeling
    [Design1.brd, Design1.sch]
2016-07-14 Labeling Cleanup
    [Design1.brd, Design1.sch]
2016-07-15 Add control for the Charges. Whoops.
    [RocketDuino.brd]
2016-07-15 Add control for the Charges. Whoops. (2)
    [RocketDuino.sch]
2016-07-15 Organize the Schematic Nicely
    [RocketDuino.sch]
2016-07-16 Fix part of ground plane
    [RocketDuino.brd]
2016-07-18 Very minor board movements
    [RocketDuino.brd]
2016-07-20 Clean schematic; Shift Board componets
    [RocketDuino.brd]
2016-07-20 Clean schematic; Shift Board componets 2
    [RocketDuino.sch]
2016-07-22 Clean up all Silkscreen Indicators
    [RocketDuino.brd, RocketDuino.sch]
2016-07-22 Made C4 Explosive
    [RocketDuino.brd, RocketDuino.sch]
2016-07-24 Seperated Serial 1 & 2
    [RocketDuino.brd, RocketDuino.sch]
2016-07-24 Add Labels for Serial
    [RocketDuino.sch]
2016-07-24 Add Labels (2)
    [RocketDuino.brd]
2016-07-24 Revert "Add Labels (2)"
    This reverts commit 649e5ca491e825c42b75eb8464ca0d71b423613b.
    [RocketDuino.brd]
2016-07-24 Revert "Revert "Add Labels (2)""
    This reverts commit 35d22b4ccda85a27ff9208a5b721f9a8abebe91e.
    [RocketDuino.brd]
2016-07-24 New DRU settings
    [RocketDuino.brd, RocketDuino.sch]
2016-07-25 Cleanups from Reddit post
    [RocketDuino.brd, RocketDuino.sch]
2016-07-26 Non-SMT I2C connector
    [RocketDuino.brd, RocketDuino.sch]
2016-07-26 Silkscreen Changes
    Also re-routed the Vsense wire
    [RocketDuino.brd, RocketDuino.sch]
2016-07-26 Minor Labeling fix
    [RocketDuino.sch]
2016-07-26 Minor Re-routes of traces
    [RocketDuino.brd]
2016-07-27 Silkscreen changes
    [RocketDuino.brd, RocketDuino.sch]
2016-07-30 Framework for flight modes
2016-07-31 Add voltage averaging
2021-10-22 First change for switching to Teensy board
2021-10-22 Groundstation code for flights 1 & 2
2021-10-22 PCB version 3.7
    [RocketDuino.brd, RocketDuino.sch]
2021-10-22 Latest version of the Teensy-based board
2021-10-22 Final v4.0 pcb version
2022-02-04 Begin work on Code for PCB 4.2
    This is the move to teensy
2022-02-14 Board updates for v4.2
2022-07-24 lora code working via aux pin

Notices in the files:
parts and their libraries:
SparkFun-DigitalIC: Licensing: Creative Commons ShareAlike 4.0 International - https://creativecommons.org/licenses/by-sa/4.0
